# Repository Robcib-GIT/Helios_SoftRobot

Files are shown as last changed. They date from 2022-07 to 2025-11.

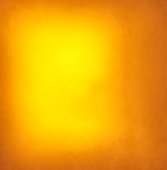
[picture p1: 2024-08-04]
Media/Imágenes/Sensor/WaveGuides/MatlabAnalysis/Core_45.png

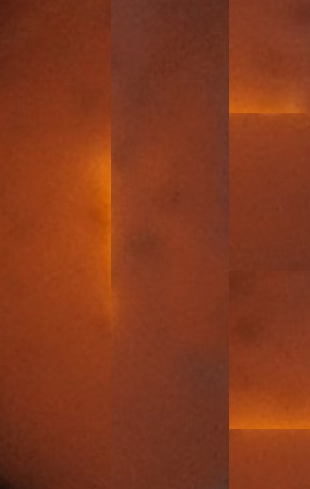
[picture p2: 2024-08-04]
Media/Imágenes/Sensor/WaveGuides/MatlabAnalysis/Cladding_60.png

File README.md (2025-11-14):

**Helios SoftRobot**
=====================================
Demo

**Installation and Configuration**
-------------------------------

### Step 1: Clone the Helios repository

Clone the Helios repository using Git:

```bash
git clone https://github.com/JaimeBravoAlgaba/Helios_SoftRobot.git
```

### Step 2: Create a ROS2 workspace

Create a directory for the ROS2 workspace and make sure it's empty:

```bash
mkdir -p helios_ws/src
```

### Step 3: Install the helios_robot package in the workspace

Copy the helios_robot package to the ROS2 workspace:

```bash
cp -r Helios_SoftRobot/Código/helios_robot helios_ws/src
cd helios_ws/src
```

### Step 4: Install the micro_ros_setup package

Clone the micro_ros_setup repository and make sure it's on the branch corresponding to your ROS2 version:

```bash
git clone https://github.com/micro-ROS/micro_ros_setup.git -b $ROS_DISTRO
cd ..
```

### Step 5: Build the workspace

Update dependencies and build the ROS2 workspace:

```bash
rosdep update && rosdep install --from-paths src --ignore-src -y
colcon build --symlink-install
source install/local_setup.bash
```

### Step 6: Create a MicroROS agent

Create a MicroROS agent and configure the environment:

```bash
ros2 run micro_ros_setup create_agent_ws.sh
ros2 run micro_ros_setup build_agent.sh
source install/local_setup.sh
```

### Step 7: Connect to the ESP32 and run the agent

Change your IP address to 192.168.2.76:



Turn on the robot if you haven't already.

**Terminal Control**
-----------
- You can use the helios_robot.sh file to automatically launch the necessary nodes:
```bash
# Launches the MicroROS agent, kinematics and pose prediction
# In the folder where the file is located, run:
./helios_robot.sh
```
and immediately after, click the RESET button on the ESP32.

- Launch the visualization node:
```bash
ros2 run helios_robot helios_robot_plot
```

- Control the cable lengths, in meters:
```bash
# [L00, L01, L02, L03, L10, L11, ... L22, L23]
ros2 topic pub --once /helios_cables_cmd std_msgs/msg/Float32MultiArray "data: [0,0,0,0,  0,0,0,0,  0,0,0,0]"
```

- Send command in theta and phi coordinates, in radians:
```bash
# [th0, th1, th2, phi0, phi1, phi2]
ros2 topic pub --once /helios_sections_cmd std_msgs/msg/Float32MultiArray "data: [0,0,0,  0,0,0]"
```

- Control the tool (value from 0 to 255):
```bash
ros2 topic pub --once /helios_tool_cmd std_msgs/msg/Int8 "data: 127"
```

### Alternative: Connect to ESP32 via USB

You can use the Helios with a USB cable:
Connect the ESP32 to the USB port and upload the esp32 project after uncommenting the lines that allow serial connection in "main.cpp" and changing board_microros_transport to "serial" in the platformio.ini file

Run the MicroROS agent with:

```bash
ros2 run micro_ros_agent micro_ros_agent serial --dev /dev/ttyUSB0
```

### Common Error Resolution

If an error appears when connecting the ESP32, make sure to grant your user access to the ttyUSB0 USB port:

1. Check the user group that has access to the port:
```bash
stat /dev/ttyUSB0
```

It should show something like: "Gid: (   20/ dialout)"

2. Add your user to the "dialout" group or whichever group appeared:
```bash
sudo usermod -a -G dialout $USER
```
3. Grant read and write permissions to the port:
```bash
sudo chmod a+rw /dev/ttyUSB0
```

After resetting the ESP32, its topics should be visible from another terminal.

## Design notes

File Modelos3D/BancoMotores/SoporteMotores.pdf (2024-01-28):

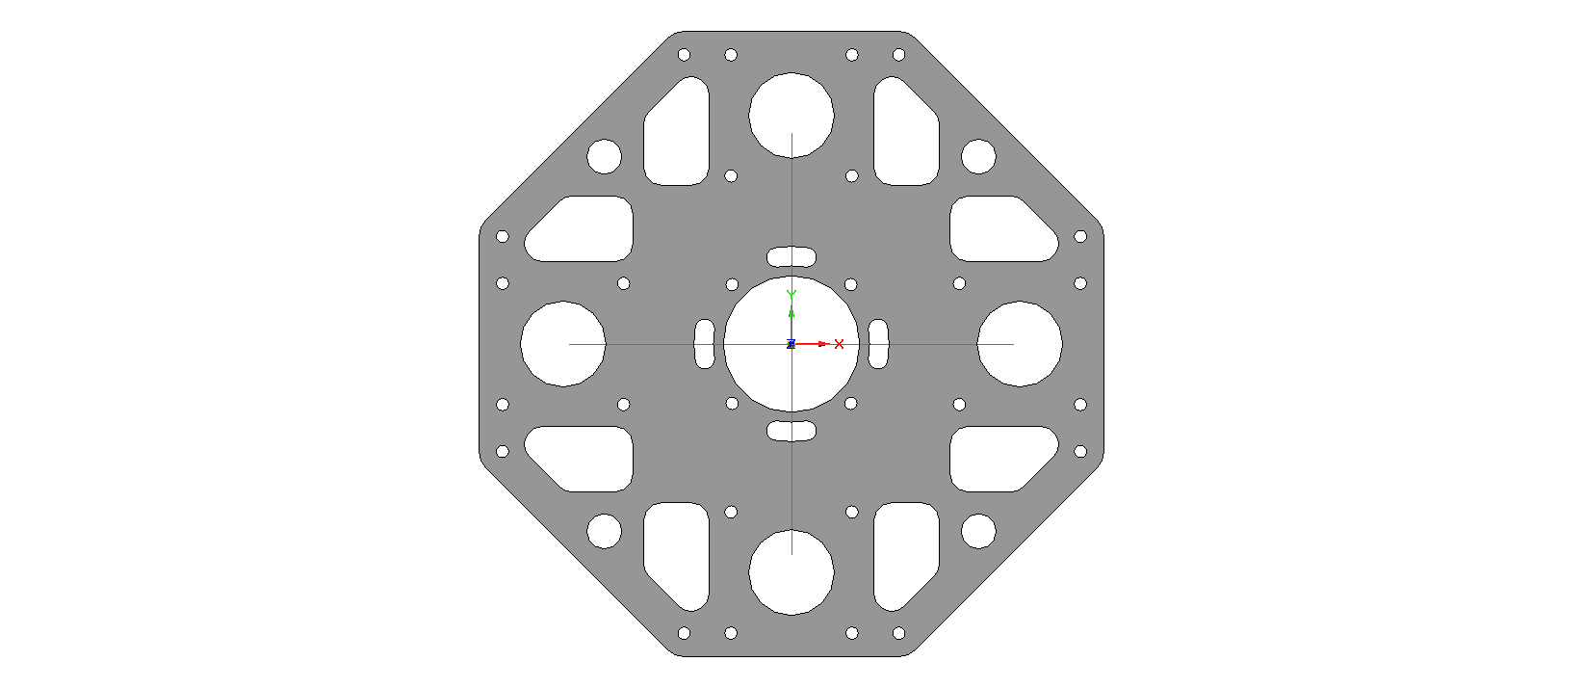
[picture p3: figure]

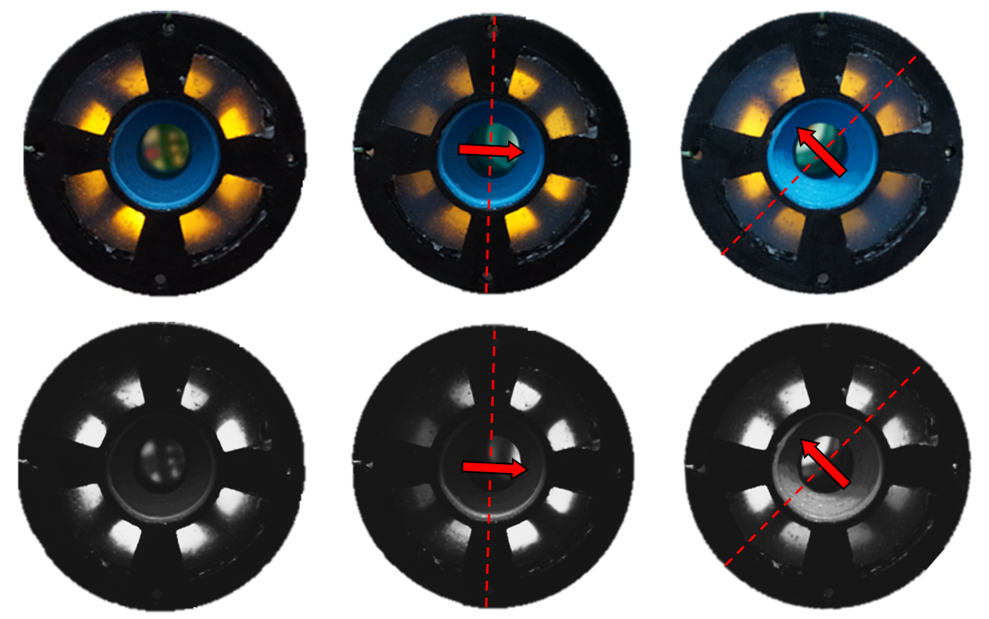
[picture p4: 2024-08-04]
Media/Imágenes/Sensor/HeliosConcept.png

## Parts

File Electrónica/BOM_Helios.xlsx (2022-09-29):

HELIOS MODULE - BOM |  |  |  |  |  |  | EMITTER PCBs |  |  |  | 20
 |  |  |  |  |  |  | RECEIVER PCBs |  |  |  | 20
COMPONENT | PCB | DESCRIPTION | DATASHEET | QTTY. PER CIRCUIT | QTTY. TOTAL | QTTY. PER ORDER | TO ORDER | ORDER PRICE | SHIPPING COSTS | TOTAL PRICE | LINK
OPA2380 | RECEIVER | Transimpedance Amplifier | opa2380 | 2 | 40 | 10 | 4 | 12.77 | 0 | 51.08 | https://es.aliexpress.com/item/1005002651519658.html?curPageLogUid=3uJtDoBWpShc
SFH2704 | RECEIVER | Photodiode | sfh2704 | 4 | 80 | 20 | 4 | 29.12 |  | 116.48 | https://es.rs-online.com/web/p/circuitos-integrados-de-sensores-biometricos/1816802
2M RESISTOR | RECEIVER | Sensing Resistance |  | 4 | 80 |  | 0 | 0 | 0
OA3400 | EMITTER | Logic Level Mosfet | oa3400 | 1 | 20 | 50 | 1 | 0.91 | 1.1 | 2.01 | https://es.aliexpress.com/item/1005004174298809.html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
2K RESISTOR | EMITTER | Pulldown Resistance |  | 1 | 20 |  | 0 | 0 | 0 | 0
241 RESISTOR | EMITTER | Current Limiting Resistance |  | 1 | 20 |  | 0 | 0 | 0 | 0

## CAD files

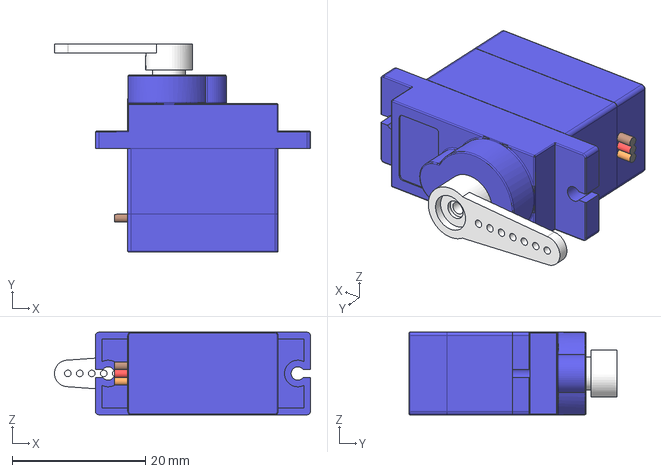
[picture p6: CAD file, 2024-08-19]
Modelos3D/Std_parts/tower-pro-sg90-micro-servo-2.snapshot.8/STEP/microservoAssembly_A3.step
38.4 x 31.3 x 12.4 mm
microservoSG90
microservoArm_A2

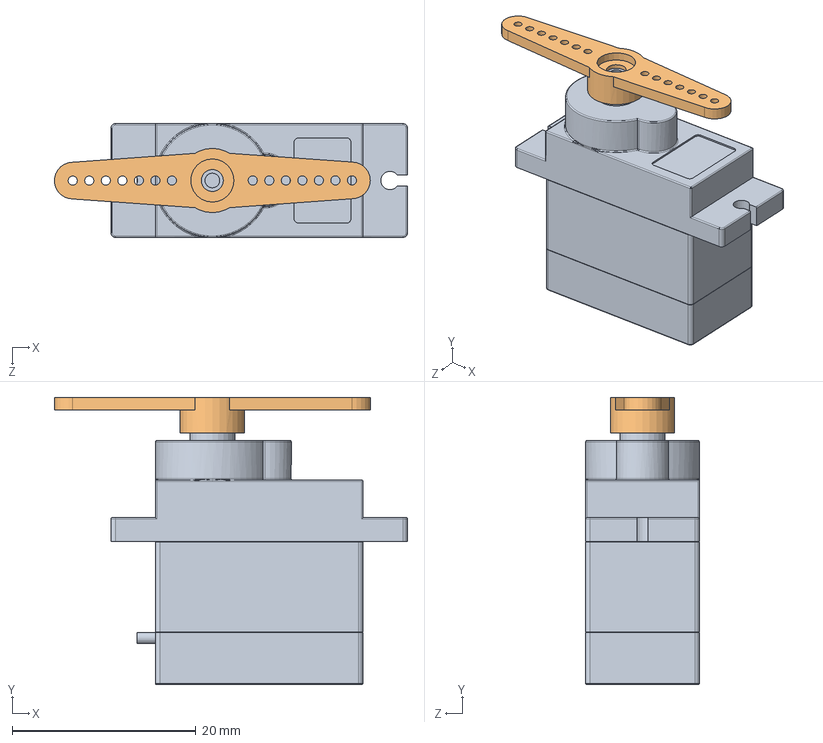
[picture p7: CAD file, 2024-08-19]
Modelos3D/Std_parts/tower-pro-sg90-micro-servo-2.snapshot.8/SLD/microservoAssembly.SLDASM
38.4 x 31.3 x 12.4 mm
microservoSG90
microservoArm

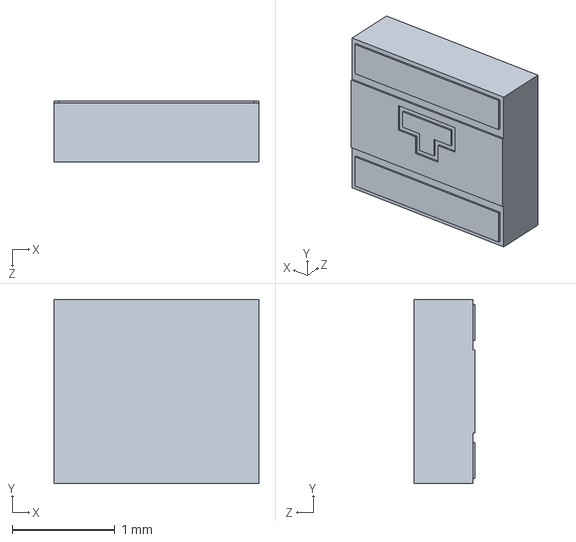
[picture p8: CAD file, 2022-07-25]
Electrónica/KicadLibs/Helios/3dmodels/SFH_2704_20190402_geometry.STEP
2.00 x 1.80 x 0.6 mm

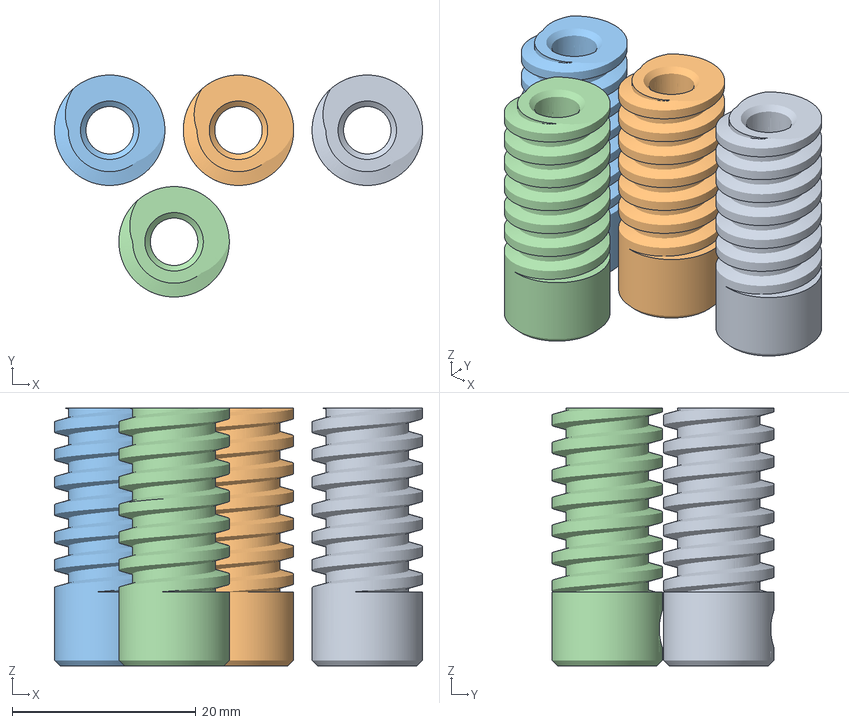
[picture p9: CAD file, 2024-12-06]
Modelos3D/Actuador/STL/CE3PRO_worm_gear.3mf
40.0 x 24.1 x 28.0 mm
worm_gear.stl x 4

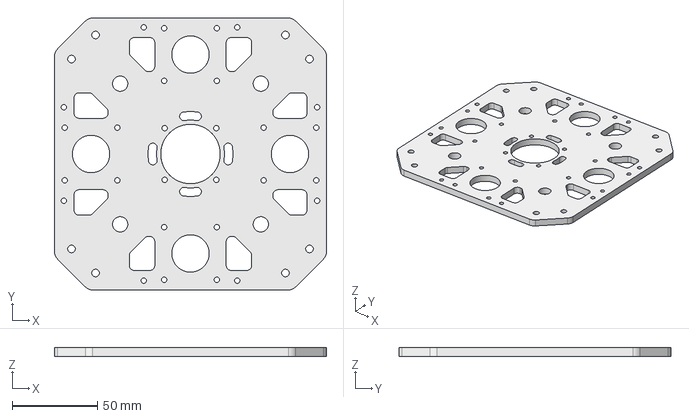
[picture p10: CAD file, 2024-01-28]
Modelos3D/BancoMotores/SoporteMotores.stp
160.0 x 160.0 x 5.00 mm

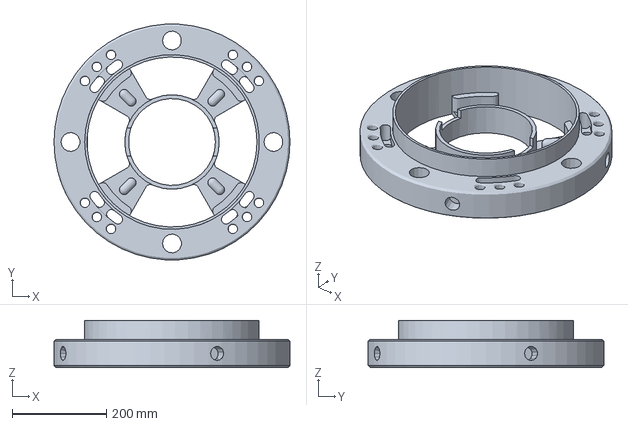
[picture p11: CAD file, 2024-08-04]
Modelos3D/Modulo_Helios/Helios_Disk/STL/MeshBody1.3mf
500.0 x 499.0 x 100.0 mm

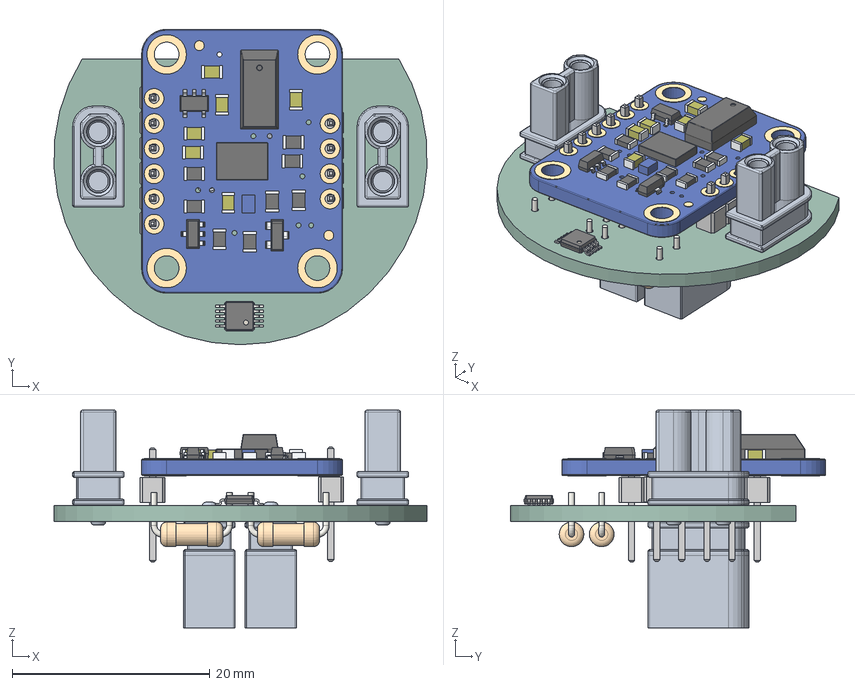
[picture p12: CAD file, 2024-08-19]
Modelos3D/Modulo_IMU/STEP/Helios_IMU_M.step
37.7 x 31.9 x 22.0 mm
ASSEMBLY x 4
(Sin guardar)
MSOP_10_3x3mm_P05mm
R_Axial_DIN0207_L63mm_D25mm_P762mm_Horizontal x 4
Helios_IMU_M_PCB

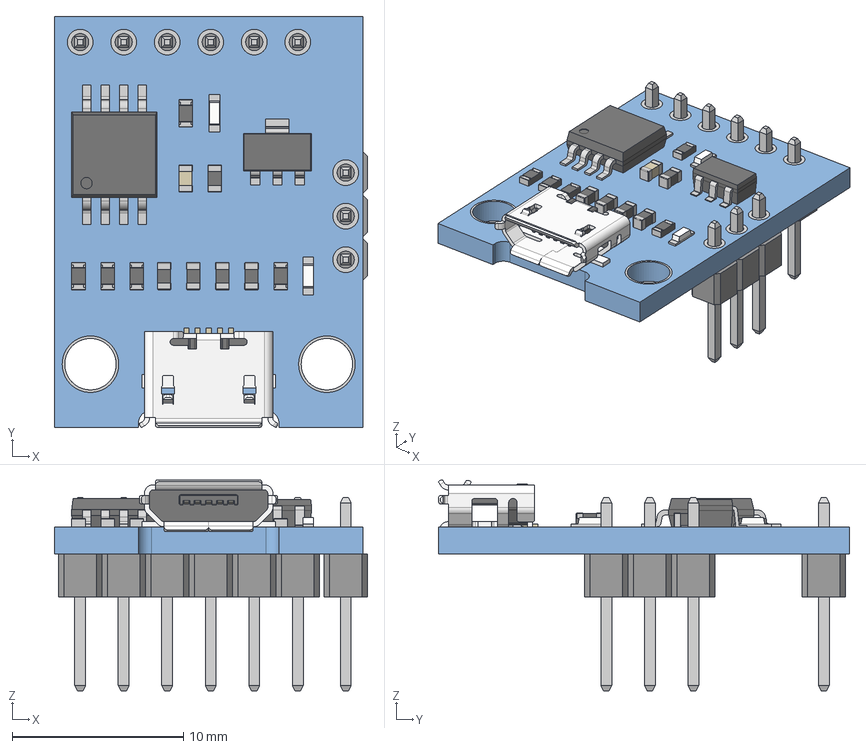
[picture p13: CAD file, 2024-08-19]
Modelos3D/Std_parts/Digispark Attiny85/STEP/Digispark Attiny85 (with pin headers).step
18.3 x 24.0 x 12.3 mm
Pads B
Pads F
Plastic
Pins
Micro USB

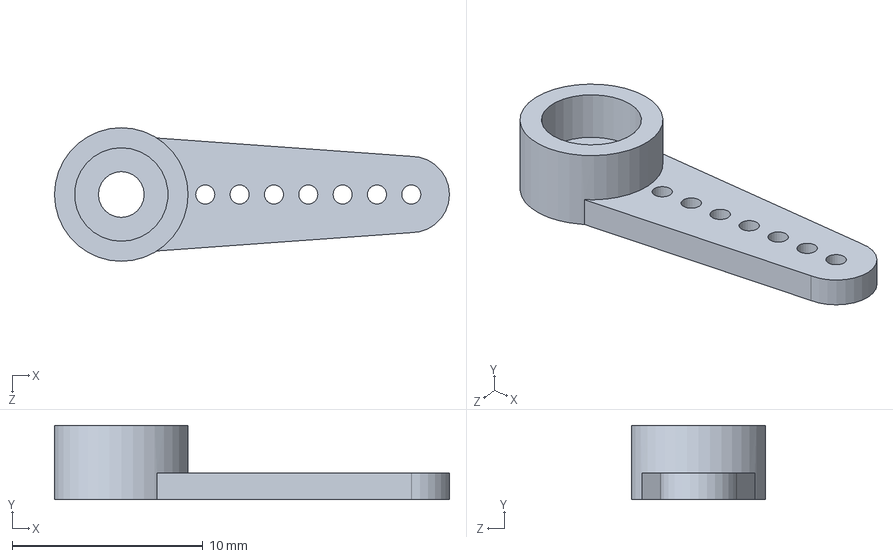
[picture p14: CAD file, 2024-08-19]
Modelos3D/Std_parts/tower-pro-sg90-micro-servo-2.snapshot.8/SLD/microservoArm.SLDPRT
20.7 x 3.90 x 7.00 mm

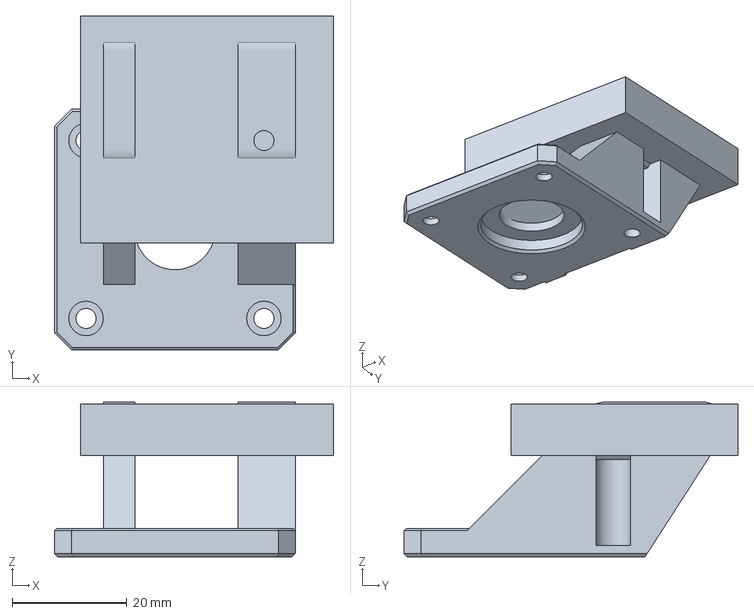
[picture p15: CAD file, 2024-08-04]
Modelos3D/Actuador/STL/CE3PRO_bastidor.3mf
48.6 x 58.2 x 27.0 mm

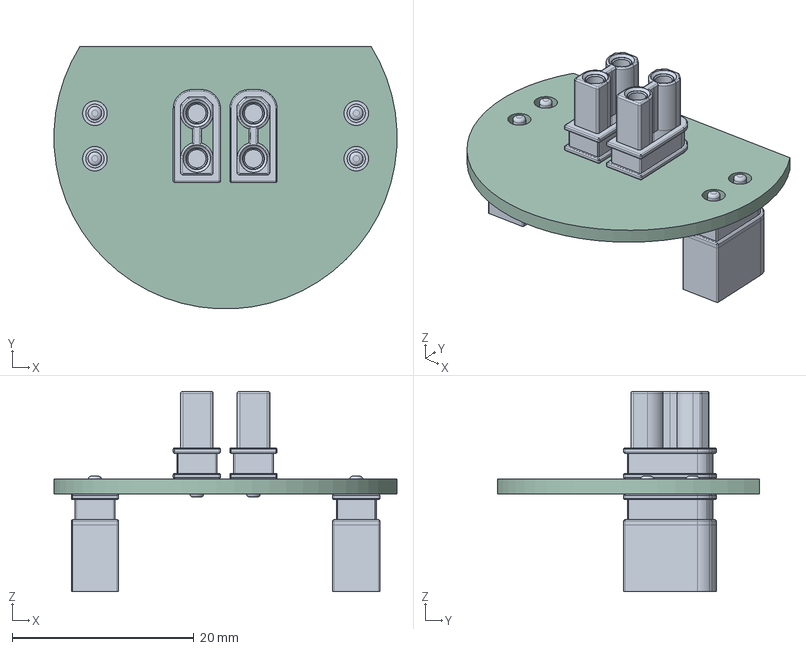
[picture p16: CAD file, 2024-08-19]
Modelos3D/Modulo_IMU/STEP/Helios_IMU_F.step
37.7 x 28.9 x 22.0 mm
ASSEMBLY x 4
Helios_IMU_F_PCB

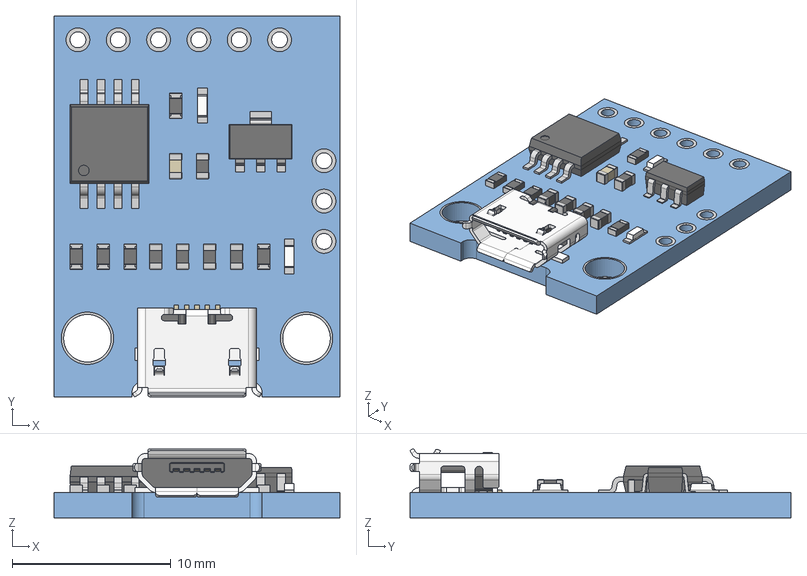
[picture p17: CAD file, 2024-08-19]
Modelos3D/Std_parts/Digispark Attiny85/STEP/Digispark Attiny85.step
18.0 x 24.0 x 4.33 mm
Pads B
Pads F
Micro USB

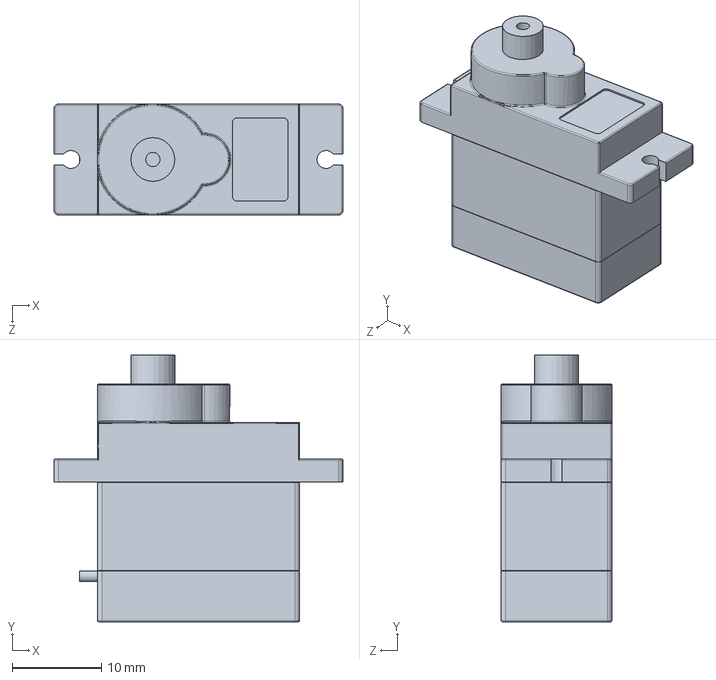
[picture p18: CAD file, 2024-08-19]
Modelos3D/Std_parts/tower-pro-sg90-micro-servo-2.snapshot.8/SLD/microservoSG90.SLDPRT
32.3 x 29.8 x 12.4 mm

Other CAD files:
Modelos3D/Std_parts/tower-pro-sg90-micro-servo-2.snapshot.8/STEP/microservoAssembly.STEP
Modelos3D/BancoMotores/SoporteMotores.dxf

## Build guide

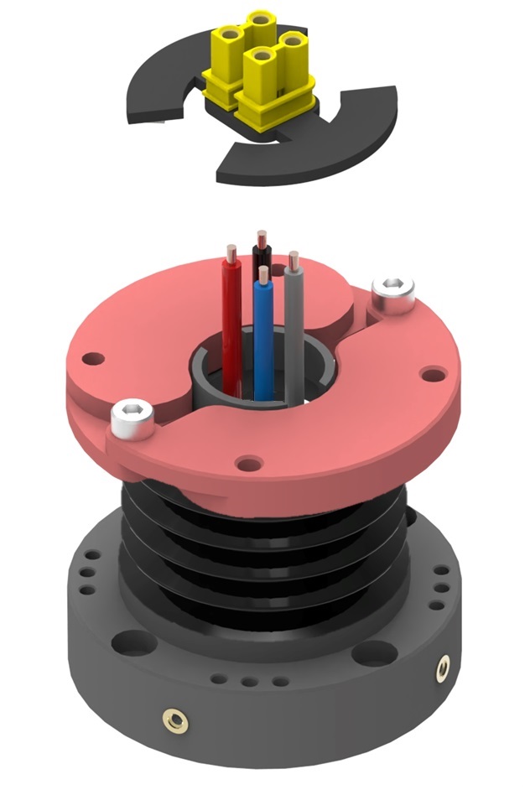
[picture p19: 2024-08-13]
Media/Imágenes/Sensor/Montaje/Paso8_A.jpg

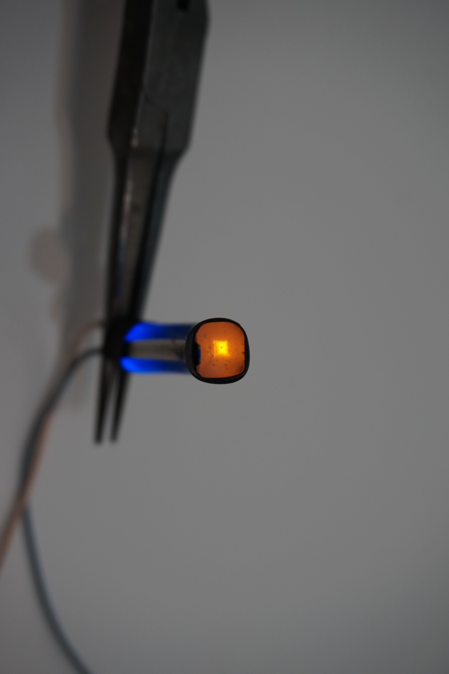
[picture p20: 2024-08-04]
Media/Imágenes/Sensor/WaveGuides/DSC03763.JPG

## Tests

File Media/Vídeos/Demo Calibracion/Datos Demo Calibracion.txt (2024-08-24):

882944,883712,882944,883456,883712,884736,885760,813056,813056,813312,813056,813312,813056,813312,813056,813824,814080,816384,818944,Motor 0 ready!
1333504,1333248,1332992,1333248,1332992,1332992,1333248,1332992,1332992,1333248,1332992,1332736,1333504,1333504,1333504,1333760,1333248,1334528,1333760,1334528,1334016,1334528,1334784,1335808,1337856,1338880,1340928,Motor 1 ready!
884992,884224,885248,884480,884480,884480,885248,885248,886272,886272,887040,887040,888320,889088,891392,Motor 2 ready!
1058304,1057536,1057792,1057536,1057536,1057280,1057792,1057536,1057792,1056768,1056768,1056512,1057792,1057536,1058048,1058048,1059584,1061376,1063168,1064192,Motor 3 ready!

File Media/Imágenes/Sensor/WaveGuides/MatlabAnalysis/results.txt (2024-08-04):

Cladding_0:126.9278
Cladding_30:97.4177
Cladding_45:86.1797
Cladding_60:76.6126
Cladding_90:45.3909
Core_0: 241.5301
Core_30:181.4205
Core_45:170.0201
Core_60:151.1259
Core_90: 94.1238

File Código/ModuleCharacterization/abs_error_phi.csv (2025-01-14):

abs_error_phi
0.26116795148977
0.04501494245398607
0.0574410258210063
0.020018695222546956
0.016932466154500503
0.013030634793675722
0.034537307033584375
0.15690723569580212
0.320014201653114
0.18757705869114538
0.09440884280808515
0.0368035878317714
0.02983785086261359
0.05580359213176056
0.0020724627015749064
0.009271791450760958
0.030697243953760056
0.019202026811451667
0.4846356430390659
0.24310086543101272
0.3646036226921556
0.20089068637257523
0.3063101115709264
0.0775011550070312
0.11384108105206836
0.1928912681536869
0.2883201347980088
0.1947866617707802
0.7724826445851589
0.21229730627382004
0.9380536972626659
0.37003076322835593
0.20886434234514173
0.03226619005276632
0.005806132350358872
0.006876534570471549
0.11219196843804813
0.2676178523780841
0.6903497831046854
0.19649137351556645
0.8923990679322125
1.8585366202787892
0.851094795704527
0.2869960545398129
0.2340101838150428
0.36409824238420363
0.619052754296189
2.541629903082378
1.4491087320107696
0.2106107012452978
0.7238617575863464
0.7805232755565461
0.26711418330450654
0.09001383140166608
0.062076002052634305
0.06536299224974185
0.1192687490245623
0.9140478307294937
0.937242972895965
0.279385629416411
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

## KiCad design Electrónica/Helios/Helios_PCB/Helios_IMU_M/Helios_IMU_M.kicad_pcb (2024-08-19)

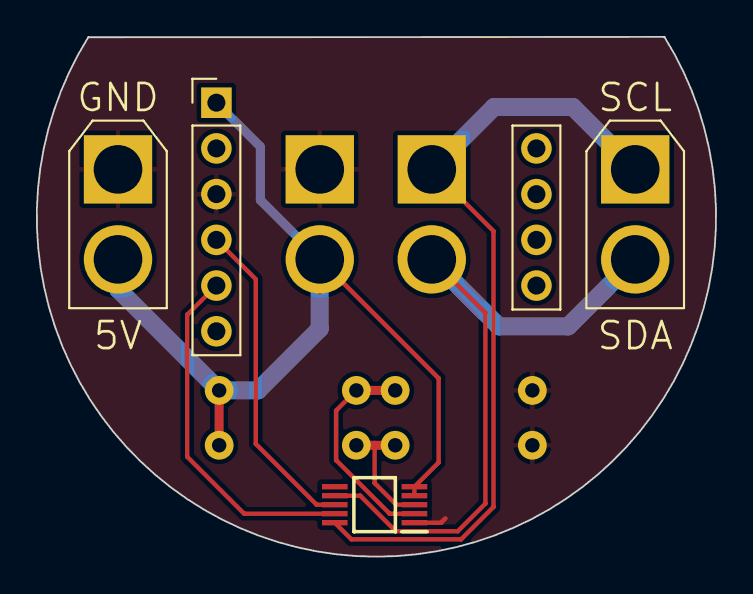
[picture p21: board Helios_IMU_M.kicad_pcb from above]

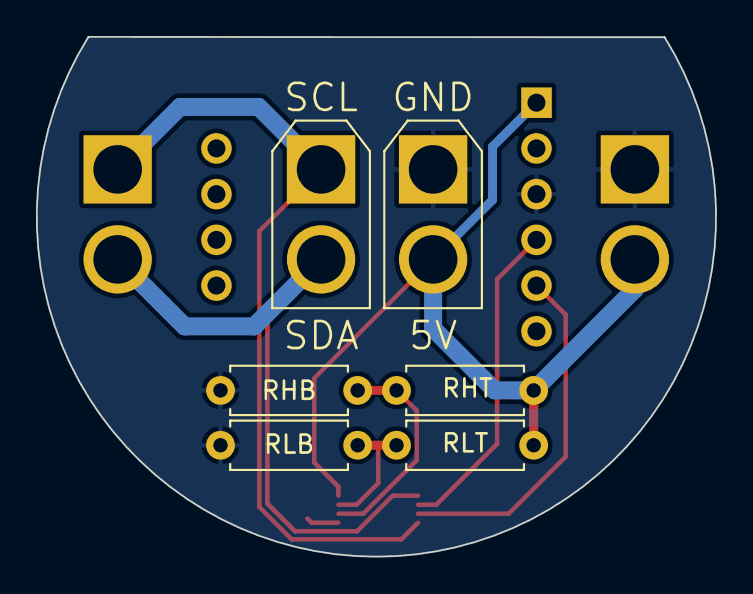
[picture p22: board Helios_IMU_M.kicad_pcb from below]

Board: 2 copper layers, 37.7 x 28.9 mm, 10 parts (6 on the bottom side), 8 nets.

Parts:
IMU1: BNO_055
J1, J2, J3, J4: Conn_01x02_Pin; XT30U-M_1x02_P5.0mm_Vertical
LTC4316: LTC4316CMS#PBF; SOP50P490X110-10N
RHB: R; R_Axial_DIN0207_L6.3mm_D2.5mm_P7.62mm_Horizontal
RHT: R; R_Axial_DIN0207_L6.3mm_D2.5mm_P7.62mm_Horizontal
RLB: R; R_Axial_DIN0207_L6.3mm_D2.5mm_P7.62mm_Horizontal
RLT: R; R_Axial_DIN0207_L6.3mm_D2.5mm_P7.62mm_Horizontal

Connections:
GND: IMU1.3 (GND), J1.1, J3.1, LTC4316.1 (GND), RHB.2, RLB.2
SCL: J2.1, J4.1, LTC4316.10 (SCLIN)
SCL_OUT: IMU1.5 (SCL), LTC4316.9 (SCLOUT)
SDA: J2.2, J4.2, LTC4316.7 (SDAIN)
SDA_OUT: IMU1.4 (SDA), LTC4316.8 (SDAOUT)
VCC: IMU1.1 (Vin), J1.2, J3.2, LTC4316.4 (VCC), LTC4316.5 (ENABLE), RHT.1, RLT.1
XORH: LTC4316.2 (XORH), RHB.1, RHT.2
XORL: LTC4316.3 (XORL), RLB.1, RLT.2

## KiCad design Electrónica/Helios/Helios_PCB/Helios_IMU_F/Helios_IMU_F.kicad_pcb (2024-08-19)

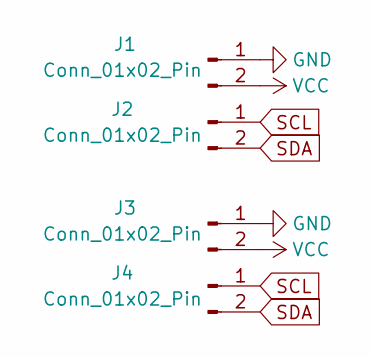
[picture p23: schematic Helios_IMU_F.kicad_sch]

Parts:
J1, J2, J3, J4: Conn_01x02_Pin; XT30U-M_1x02_P5.0mm_Vertical

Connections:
GND: J1.1, J3.1
SCL: J2.1, J4.1
SDA: J2.2, J4.2
VCC: J1.2, J3.2

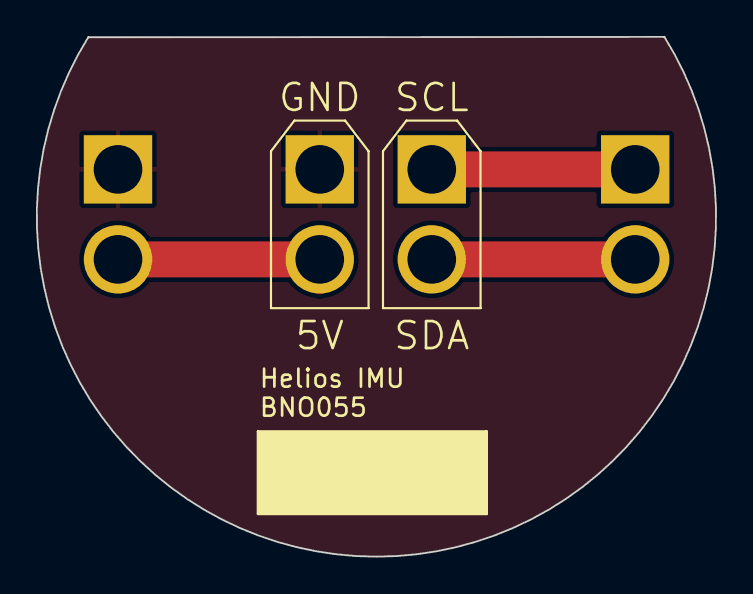
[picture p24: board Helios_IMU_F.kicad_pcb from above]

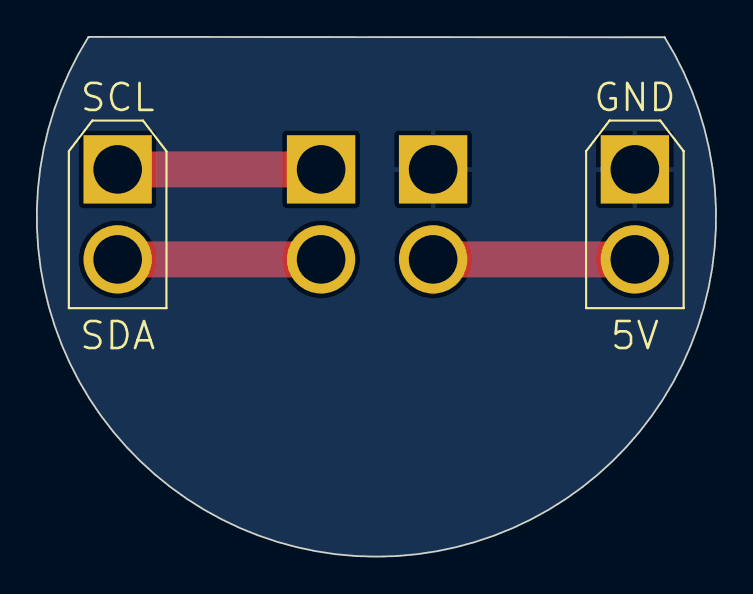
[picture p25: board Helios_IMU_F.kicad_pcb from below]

Board: 2 copper layers, 37.7 x 28.9 mm, 4 parts (2 on the bottom side), 4 nets.

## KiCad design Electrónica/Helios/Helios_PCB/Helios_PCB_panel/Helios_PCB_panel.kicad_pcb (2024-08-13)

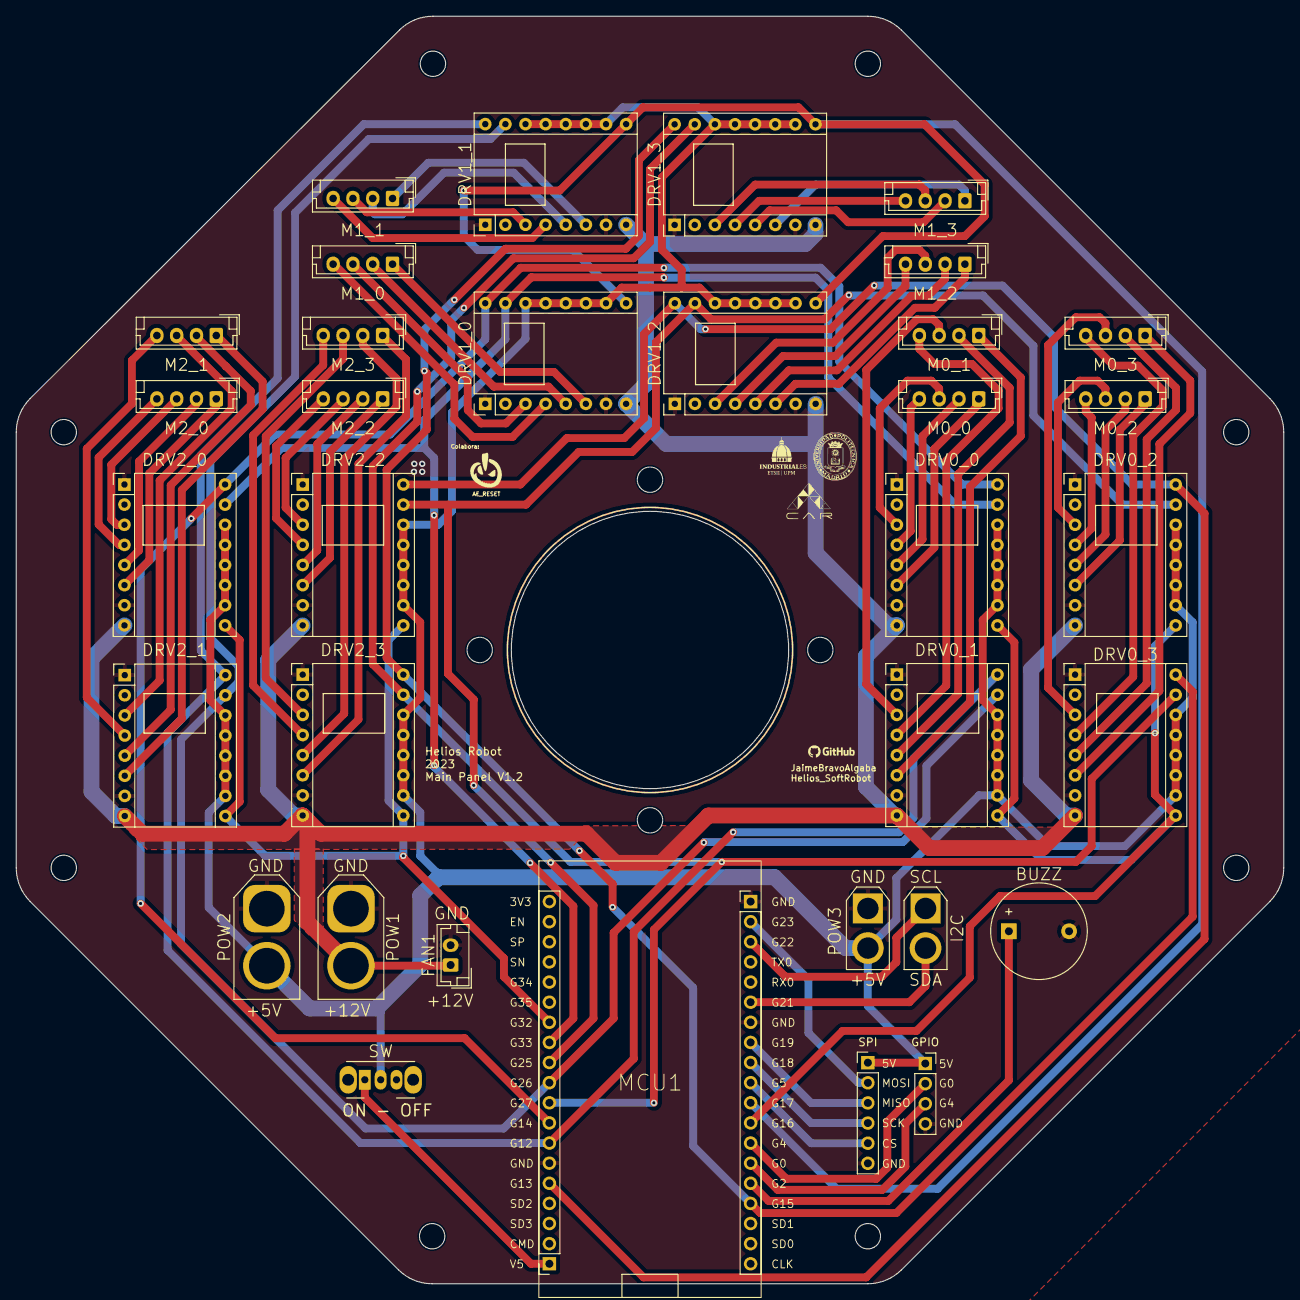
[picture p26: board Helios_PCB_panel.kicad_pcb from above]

Board: 2 copper layers, 160.0 x 160.0 mm, 46 parts (0 on the bottom side), 72 nets.

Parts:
BUZZ: Buzzer; Buzzer_12x9.5RM7.6
DRV0_0, DRV0_1, DRV0_2, DRV0_3, DRV1_0, DRV1_1, DRV1_2, DRV1_3, DRV2_0, DRV2_1, DRV2_2, DRV2_3: Pololu_Breakout_DRV8825; Pololu_Breakout-16_15.2x20.3mm
FAN1: 12VDC; JST_EH_B2B-EH-A_1x02_P2.50mm_Vertical
GPIO: Conn_01x04_Pin; PinSocket_1x04_P2.54mm_Vertical
H1, H2, H3, H4, H5, H6, H7, H8, H9, H10, H11, H12: MountingHole; MountingHole_3.2mm_M3
I2C: I2C1; XT30U-F_1x02_P5.0mm_Vertical
M0_0, M0_1, M0_2, M0_3, M1_0, M1_1, M1_2, M1_3, M2_0, M2_1, M2_2, M2_3: Conn_01x04_Pin; JST_EH_B4B-EH-A_1x04_P2.50mm_Vertical
MCU1: NodeMCU
POW1: 12VDC; XT60-M_1x02_P7.20mm_Vertical
POW2: 5VDC; XT60-M_1x02_P7.20mm_Vertical
POW3: 5VDC; XT30U-F_1x02_P5.0mm_Vertical
SPI: Conn_01x06_Pin; PinHeader_1x06_P2.54mm_Vertical
SW: SW_SPDT; SW_CuK_OS102011MA1QN1_SPDT_Angled

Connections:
+5V: DRV0_0.10 (M0), DRV0_0.11 (M1), DRV0_0.12 (M2), DRV0_0.13 (~RST), DRV0_0.14 (~SLP), DRV0_1.10 (M0), DRV0_1.11 (M1), DRV0_1.12 (M2), DRV0_1.13 (~RST), DRV0_1.14 (~SLP), DRV0_2.10 (M0), DRV0_2.11 (M1), DRV0_2.12 (M2), DRV0_2.13 (~RST), DRV0_2.14 (~SLP), DRV0_3.10 (M0), DRV0_3.11 (M1), DRV0_3.12 (M2), DRV0_3.13 (~RST), DRV0_3.14 (~SLP), DRV1_0.10 (M0), DRV1_0.11 (M1), DRV1_0.12 (M2), DRV1_0.13 (~RST), DRV1_0.14 (~SLP), DRV1_1.10 (M0), DRV1_1.11 (M1), DRV1_1.12 (M2), DRV1_1.13 (~RST), DRV1_1.14 (~SLP), DRV1_2.10 (M0), DRV1_2.11 (M1), DRV1_2.12 (M2), DRV1_2.13 (~RST), DRV1_2.14 (~SLP), DRV1_3.10 (M0), DRV1_3.11 (M1), DRV1_3.12 (M2), DRV1_3.13 (~RST), DRV1_3.14 (~SLP), DRV2_0.10 (M0), DRV2_0.11 (M1), DRV2_0.12 (M2), DRV2_0.13 (~RST), DRV2_0.14 (~SLP), DRV2_1.10 (M0), DRV2_1.11 (M1), DRV2_1.12 (M2), DRV2_1.13 (~RST), DRV2_1.14 (~SLP), DRV2_2.10 (M0), DRV2_2.11 (M1), DRV2_2.12 (M2), DRV2_2.13 (~RST), DRV2_2.14 (~SLP), DRV2_3.10 (M0), DRV2_3.11 (M1), DRV2_3.12 (M2), DRV2_3.13 (~RST), DRV2_3.14 (~SLP), GPIO.1, POW2.2, POW3.2, SPI.1, SW.2 (B)
+12V: DRV0_0.8 (VMOT), DRV0_1.8 (VMOT), DRV0_2.8 (VMOT), DRV0_3.8 (VMOT), DRV1_0.8 (VMOT), DRV1_1.8 (VMOT), DRV1_2.8 (VMOT), DRV1_3.8 (VMOT), DRV2_0.8 (VMOT), DRV2_1.8 (VMOT), DRV2_2.8 (VMOT), DRV2_3.8 (VMOT), FAN1.1, POW1.2
BUZZ: BUZZ.1 (-), MCU1.24 (G2)
CS: MCU1.29 (G5), SPI.5
D0: DRV0_0.16 (DIR), DRV1_0.16 (DIR), DRV2_0.16 (DIR), MCU1.12 (G14)
D1: DRV0_1.16 (DIR), DRV1_1.16 (DIR), DRV2_1.16 (DIR), MCU1.13 (G12)
D2: DRV0_2.16 (DIR), DRV1_2.16 (DIR), DRV2_2.16 (DIR), MCU1.15 (G13)
D3: DRV0_3.16 (DIR), DRV1_3.16 (DIR), DRV2_3.16 (DIR), MCU1.23 (G15)
EN0: DRV0_0.9 (~EN), DRV0_1.9 (~EN), DRV0_2.9 (~EN), DRV0_3.9 (~EN), MCU1.27 (G16)
EN1: DRV1_0.9 (~EN), DRV1_1.9 (~EN), DRV1_2.9 (~EN), DRV1_3.9 (~EN), MCU1.28 (G17)
EN2: DRV2_0.9 (~EN), DRV2_1.9 (~EN), DRV2_2.9 (~EN), DRV2_3.9 (~EN), MCU1.7 (G32)
GND: BUZZ.2 (+), DRV0_0.1 (GND), DRV0_0.7 (GND), DRV0_1.1 (GND), DRV0_1.7 (GND), DRV0_2.1 (GND), DRV0_2.7 (GND), DRV0_3.1 (GND), DRV0_3.7 (GND), DRV1_0.1 (GND), DRV1_0.7 (GND), DRV1_1.1 (GND), DRV1_1.7 (GND), DRV1_2.1 (GND), DRV1_2.7 (GND), DRV1_3.1 (GND), DRV1_3.7 (GND), DRV2_0.1 (GND), DRV2_0.7 (GND), DRV2_1.1 (GND), DRV2_1.7 (GND), DRV2_2.1 (GND), DRV2_2.7 (GND), DRV2_3.1 (GND), DRV2_3.7 (GND), FAN1.2, GPIO.4, MCU1.14 (GND), MCU1.32 (GND), MCU1.38 (GND), POW1.1, POW2.1, POW3.1, SPI.6
MISO: MCU1.31 (G19), SPI.3
MOSI: MCU1.37 (G23), SPI.2
unnamed: DRV0_0.4 (A1), M0_0.4
unnamed: DRV0_0.3 (A2), M0_0.3
unnamed: DRV0_0.5 (B1), M0_0.2
unnamed: DRV0_0.6 (B2), M0_0.1
unnamed: DRV0_1.4 (A1), M0_1.4
unnamed: DRV0_1.3 (A2), M0_1.3
unnamed: DRV0_1.5 (B1), M0_1.2
unnamed: DRV0_1.6 (B2), M0_1.1
unnamed: DRV0_2.4 (A1), M0_2.4
unnamed: DRV0_2.3 (A2), M0_2.3
unnamed: DRV0_2.5 (B1), M0_2.2
unnamed: DRV0_2.6 (B2), M0_2.1
unnamed: DRV0_3.4 (A1), M0_3.4
unnamed: DRV0_3.3 (A2), M0_3.3
unnamed: DRV0_3.5 (B1), M0_3.2
unnamed: DRV0_3.6 (B2), M0_3.1
unnamed: DRV1_0.4 (A1), M1_0.4
unnamed: DRV1_0.3 (A2), M1_0.3
unnamed: DRV1_0.5 (B1), M1_0.2
unnamed: DRV1_0.6 (B2), M1_0.1
unnamed: DRV1_1.4 (A1), M1_1.4
unnamed: DRV1_1.3 (A2), M1_1.3
unnamed: DRV1_1.5 (B1), M1_1.2
unnamed: DRV1_1.6 (B2), M1_1.1
unnamed: DRV1_2.4 (A1), M1_2.4
unnamed: DRV1_2.3 (A2), M1_2.3
unnamed: DRV1_2.5 (B1), M1_2.2
unnamed: DRV1_2.6 (B2), M1_2.1
unnamed: DRV1_3.4 (A1), M1_3.4
unnamed: DRV1_3.3 (A2), M1_3.3
unnamed: DRV1_3.5 (B1), M1_3.2
unnamed: DRV1_3.6 (B2), M1_3.1
unnamed: DRV2_0.4 (A1), M2_0.4
unnamed: DRV2_0.3 (A2), M2_0.3
unnamed: DRV2_0.5 (B1), M2_0.2
unnamed: DRV2_0.6 (B2), M2_0.1
unnamed: DRV2_1.4 (A1), M2_1.4
unnamed: DRV2_1.3 (A2), M2_1.3
unnamed: DRV2_1.5 (B1), M2_1.2
unnamed: DRV2_1.6 (B2), M2_1.1
unnamed: DRV2_2.4 (A1), M2_2.4
unnamed: DRV2_2.3 (A2), M2_2.3
unnamed: DRV2_2.5 (B1), M2_2.2
unnamed: DRV2_2.6 (B2), M2_2.1
unnamed: DRV2_3.4 (A1), M2_3.4
unnamed: DRV2_3.3 (A2), M2_3.3
unnamed: DRV2_3.5 (B1), M2_3.2
unnamed: DRV2_3.6 (B2), M2_3.1
unnamed: GPIO.2, MCU1.26 (G4)
unnamed: GPIO.3, MCU1.25 (G0)
unnamed: MCU1.19 (V5), SW.1 (A)
S0: DRV0_0.15 (STEP), DRV1_0.15 (STEP), DRV2_0.15 (STEP), MCU1.8 (G33)
S1: DRV0_1.15 (STEP), DRV1_1.15 (STEP), DRV2_1.15 (STEP), MCU1.10 (G26)
S2: DRV0_2.15 (STEP), DRV1_2.15 (STEP), DRV2_2.15 (STEP), MCU1.9 (G25)
S3: DRV0_3.15 (STEP), DRV1_3.15 (STEP), DRV2_3.15 (STEP), MCU1.11 (G27)
SCK: MCU1.30 (G18), SPI.4
SCL: I2C.1, MCU1.36 (G22)
SDA: I2C.2, MCU1.33 (G21)

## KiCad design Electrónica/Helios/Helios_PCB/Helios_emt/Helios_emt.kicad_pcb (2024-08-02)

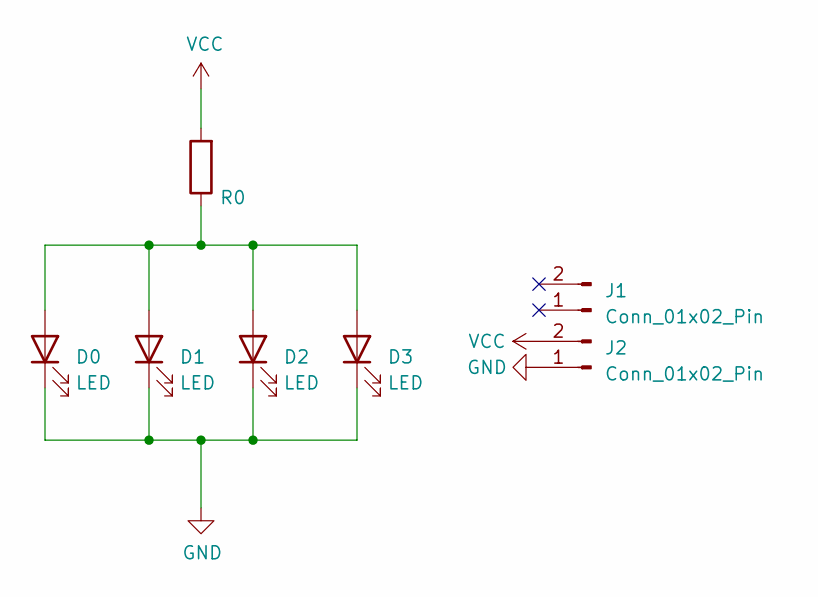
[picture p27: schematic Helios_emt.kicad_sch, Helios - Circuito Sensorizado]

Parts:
D0, D1, D2, D3: LED; LED_PLCC-2
J1, J2: Conn_01x02_Pin; AMASS_XT30U-F_1x02_P5.0mm_Vertical
R0: RL; R_0805_2012Metric

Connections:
GND: D0.1 (K), D1.1 (K), D2.1 (K), D3.1 (K), J2.1
unnamed: D0.2 (A), D1.2 (A), D2.2 (A), D3.2 (A), R0.1
VCC: J2.2, R0.2

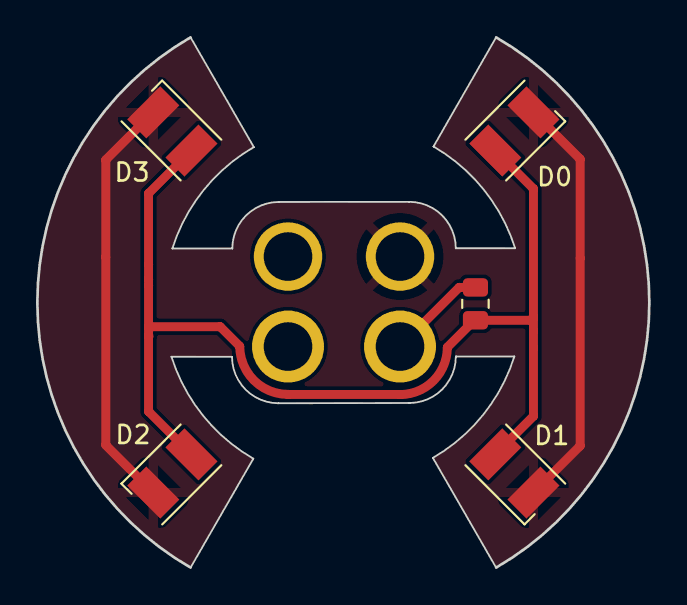
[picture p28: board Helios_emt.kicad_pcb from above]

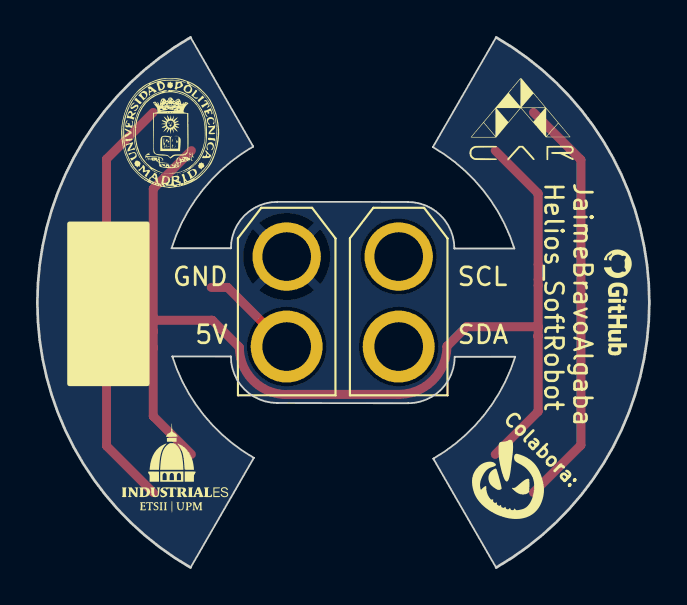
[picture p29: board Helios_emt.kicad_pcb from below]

Board: 2 copper layers, 34.0 x 29.5 mm, 7 parts (2 on the bottom side), 3 nets.

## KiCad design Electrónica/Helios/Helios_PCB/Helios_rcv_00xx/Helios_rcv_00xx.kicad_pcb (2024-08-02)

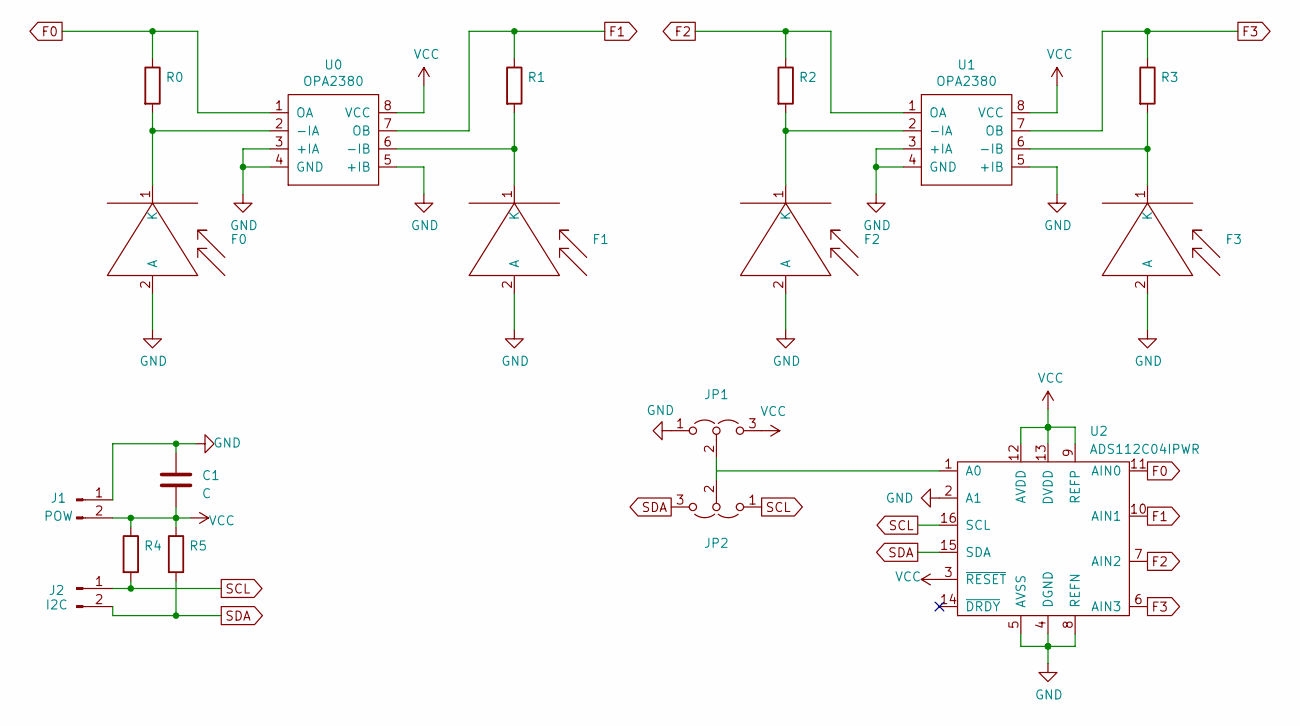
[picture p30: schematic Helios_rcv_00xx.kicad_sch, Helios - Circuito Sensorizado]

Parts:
C1: C; C_0805_2012Metric
F0, F1, F2, F3: SFH2704; SFH2704_Photodiode
J1: POW; XT30U-M_1x02_P5.0mm_Vertical
J2: I2C; XT30U-M_1x02_P5.0mm_Vertical
JP1, JP2: Jumper_3_Open; SolderJumper-3_P1.3mm_Open_Pad1.0x1.5mm
R0, R1, R2, R3, R4, R5: Rf; R_0805_2012Metric
U0, U1: OPA2380
U2: ADS112C04IPWR; TSSOP-16_4.4x5mm_P0.65mm

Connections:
F0: R0.1, U0.1 (OA), U2.11 (AIN0)
F1: R1.1, U0.7 (OB), U2.10 (AIN1)
F2: R2.1, U1.1 (OA), U2.7 (AIN2)
F3: R3.1, U1.7 (OB), U2.6 (AIN3)
GND: C1.1, F0.2 (A), F1.2 (A), F2.2 (A), F3.2 (A), J1.1, JP1.1 (A), U0.3 (+IA), U0.4 (GND), U0.5 (+IB), U1.3 (+IA), U1.4 (GND), U1.5 (+IB), U2.2 (A1), U2.4 (DGND), U2.5 (AVSS), U2.8 (REFN)
unnamed: F0.1 (K), R0.2, U0.2 (-IA)
unnamed: F1.1 (K), R1.2, U0.6 (-IB)
unnamed: F2.1 (K), R2.2, U1.2 (-IA)
unnamed: F3.1 (K), R3.2, U1.6 (-IB)
unnamed: JP1.2 (C), JP2.2 (C)
SCL: J2.1, JP2.1 (A), R4.2, U2.16 (SCL)
SDA: J2.2, JP2.3 (B), R5.2, U2.15 (SDA)
VCC: C1.2, J1.2, JP1.3 (B), R4.1, R5.1, U0.8 (VCC), U1.8 (VCC), U2.3 (~RESET), U2.9 (REFP), U2.12 (AVDD), U2.13 (DVDD)

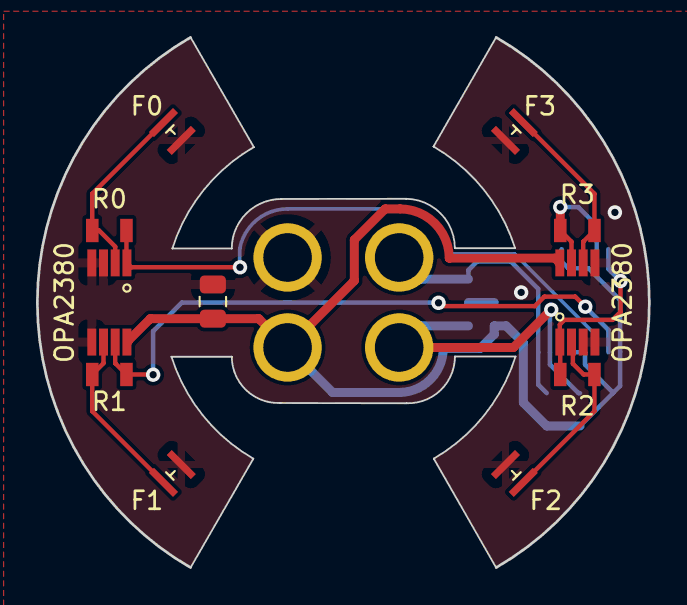
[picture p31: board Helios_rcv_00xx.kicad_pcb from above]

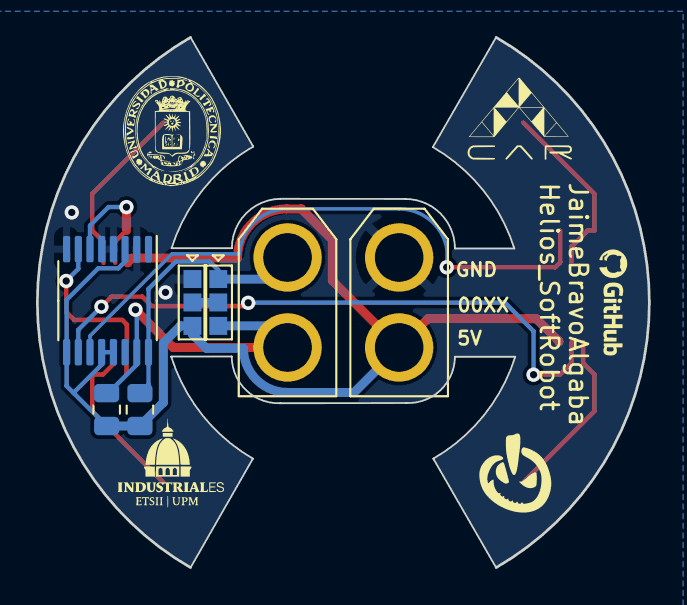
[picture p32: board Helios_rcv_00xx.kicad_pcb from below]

Board: 2 copper layers, 34.0 x 29.5 mm, 18 parts (7 on the bottom side), 13 nets.

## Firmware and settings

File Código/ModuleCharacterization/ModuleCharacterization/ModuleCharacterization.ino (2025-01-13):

#include <Wire.h>
#include "CNC_Shield_UNO.h"
#include "Helios.h"

#define HELIOS_ADDR 0x4A
#define IMU_0_ADDR 0x08
#define TCA_ADDR 0x70

HeliosSensor helios;
Adafruit_VL6180X tof = Adafruit_VL6180X();

uint32_t h[4] = {0, 0, 0, 0}; // Helios module measurement
uint8_t l_tofs[4]; // TOF modules measurement

float cableLengths[4] = {SEGMENTS_LEN, SEGMENTS_LEN, SEGMENTS_LEN, SEGMENTS_LEN};
sensors_event_t orientationData;

CoordsPCC coords_ref;
CoordsPCC coords_meas;

bool succ_init = true;

void move(CoordsPCC c) {
  float l_ref[4] = {0, 0, 0, 0};
  long dn[4] = {0, 0, 0, 0};
  
  for (uint8_t i = 0; i < 4; ++i) {
    l_ref[i] = cableIKine(c, i);
    dn[i] = length2steps(l_ref[i] - cableLengths[i]);
    cableLengths[i] = l_ref[i];
  }
  stepParallel(dn);
}

void calibrateCables() {
  print_info("Starting calibration... ");
  
  // De-tension the cables lengthening them
  long dn[4] = {length2steps(0.005), length2steps(0.005), length2steps(0.005), length2steps(0.005)};
  stepParallel(dn);
  
  memmove(l_tofs, readTOFs(), sizeof(l_tofs) * sizeof(uint8_t));
  long l_tofs_init[4];
  for (uint8_t i = 0; i < 4; ++i) {
    dn[i] = 0;
  }
  
  for(uint8_t i = 0; i < 4; ++i) {
    dn[i] = length2steps(-0.001);
    l_tofs_init[i] = l_tofs[i];

    while (abs(l_tofs[i] - l_tofs_init[i]) < 3) {
      stepParallel(dn);
      memmove(l_tofs, readTOFs(), sizeof(l_tofs) * sizeof(uint8_t));
    }
    dn[i] = 0;
  }

  coords_meas = tofs2pcc(l_tofs[0], l_tofs[1], l_tofs[2], l_tofs[3]);
}

void printData() {
  // Print TOF data
  Serial.print("{\"TOFS\":[");
  for (uint8_t i = 0; i < 3; ++i) {
    Serial.print(l_tofs[i]);
    Serial.print(",");
  }
  Serial.print(l_tofs[3]);

  // Print Helios data
  Serial.print("], \"HELIOS\":[");
  for (uint8_t i = 0; i < 4; ++i) {
    Serial.print(h[i]);
    if (i < 3) {
      Serial.print(",");
    } else {
      Serial.print("]}\n");
    }
  }
}

void setup() {
  setupCNC();

  Serial.begin(115200);
  while (!Serial) delay(10);  // Wait for serial port to open
  Wire.begin();

  // HELIOS INIT
  print_info("Initializing Helios module on address ");
  print_info(String(HELIOS_ADDR));
  print_info("\n");
  while (!helios.begin(HELIOS_ADDR)) {
    print_info(F("Helios Module not detected. Retrying...\n"));
    delay(500);
  }

  helios.configureADCmode(ADS122C04_RAW_MODE);
  helios.setGain(ADS122C04_GAIN_128);
  helios.setConversionMode(ADS122C04_CONVERSION_MODE_CONTINUOUS);
  helios.start();

  print_info("OK\n");

  // TCA9548A Initialization
  print_info("Initializing TCA9548A with address ");
  print_info(String(TCA_ADDR));
  print_info("\n");
  
  for (uint8_t i = 0; i < 4; ++i) {
    tcaSelect(i);
    if (!tof.begin()) {
      print_info(F("\tFailed to boot TOF on channel "));
      print_info(String(i));
      print_info("\n");
      succ_init = false;
    } else {
      print_info(F("\tSuccess booting TOF on channel "));
      print_info(String(i));
      print_info("\n");
    }
  }
  print_info("OK\n");

  if (succ_init) {  
    print_info("\nInitialization successful!\n");
  } else {
    print_info("\nInitialization failed!\n");
    while (1);
  }

  Serial.println("START");
}

void loop() {  
  if (Serial.available() > 0) {
    String cmd = Serial.readStringUntil('\n');

    if (cmd == "HELLO") {
      Serial.println("OK");
      return;
    }
    
    else if (cmd == "CALIBRATE") {
      calibrateCables();
      Serial.println("OK");
    }
    
    else {
      float dl[4];
      long dn[4];

      if (cmd.startsWith("DELTA_LEN:")) {
        cmd.remove(0, String("DELTA_LEN:").length());

        int firstComma  = cmd.indexOf(',');
        int secondComma = cmd.indexOf(',', firstComma + 1);
        int thirdComma  = cmd.indexOf(',', secondComma + 1);

        int commas[3];
        commas[0] = cmd.indexOf(',');        
        commas[1] = cmd.indexOf(',', commas[0] + 1);
        commas[2] = cmd.indexOf(',', commas[1] + 1);

        dl[0] = cmd.substring(0, commas[0]).toFloat();
        dn[0] = length2steps(dl[0]);
        for (int i = 1; i < 4; ++i) {
          dl[i] = cmd.substring(commas[i - 1] + 1, (i < 3) ? commas[i] : cmd.length()).toFloat();
          dn[i] = length2steps(dl[i]);
          cableLengths[i] = dl[i] + cableLengths[i];
        }
      }

      else if (cmd.startsWith("DELTA_STEPS:")) {
        cmd.remove(0, String("DELTA_STEPS:").length());

        int firstComma  = cmd.indexOf(',');
        int secondComma = cmd.indexOf(',', firstComma + 1);
        int thirdComma  = cmd.indexOf(',', secondComma + 1);
        
        int commas[3];
        commas[0] = cmd.indexOf(',');
        commas[1] = cmd.indexOf(',', commas[0] + 1);
        commas[2] = cmd.indexOf(',', commas[1] + 1);

        dn[0] = cmd.substring(0, commas[0]).toInt();
        for (int i = 1; i < 4; ++i) {
          dn[i] = cmd.substring(commas[i - 1] + 1, (i < 3) ? commas[i] : cmd.length()).toInt();
          dl[i] = steps2length(dn[i]);
          cableLengths[i] = dl[i] + cableLengths[i];
        }   
      }

      else if (cmd.startsWith("DELTA_PCC:")) {
        cmd.remove(0, String("DELTA_PCC:").length());

        int firstComma  = cmd.indexOf(',');
        int secondComma = cmd.indexOf(',', firstComma + 1);
        int thirdComma  = cmd.indexOf(',', secondComma + 1);

        coords_ref.theta = cmd.substring(0, firstComma).toFloat() + coords_meas.theta;
        coords_ref.phi = cmd.substring(firstComma + 1, secondComma).toFloat() + coords_meas.phi;
        coords_ref.length = cmd.substring(secondComma + 1, thirdComma).toFloat() + coords_meas.length;
        
        for (uint8_t i = 0; i < 4; ++i) {
          dl[i] = cableIKine(coords_ref, i) - cableLengths[i];
          dn[i] = length2steps(dl[i]);
          cableLengths[i] = dl[i] + cableLengths[i];
        }
      }

      else if (cmd.startsWith("REF_PCC:")) {
        cmd.remove(0, String("REF_PCC:").length());

        int firstComma  = cmd.indexOf(',');
        int secondComma = cmd.indexOf(',', firstComma + 1);
        int thirdComma  = cmd.indexOf(',', secondComma + 1);

        coords_ref.theta = cmd.substring(0, firstComma).toFloat();
        coords_ref.phi = cmd.substring(firstComma + 1, secondComma).toFloat();
        coords_ref.length = cmd.substring(secondComma + 1, thirdComma).toFloat();
        
        for (uint8_t i = 0; i < 4; ++i) {
          dl[i] = cableIKine(coords_ref, i) - cableLengths[i];
          dn[i] = length2steps(dl[i]);
          cableLengths[i] = dl[i] + cableLengths[i];
        }
      }

      else if (cmd.startswith("REF_LEN:")) {
        cmd.remove(0, String("REF_LEN:").length());

        int firstComma  = cmd.indexOf(',');
        int secondComma = cmd.indexOf(',', firstComma + 1);
        int thirdComma  = cmd.indexOf(',', secondComma + 1);

        dl[0] = cmd.substring(0, firstComma).toFloat() - cableLengths[0];
        dn[0] = length2steps(dl[0]);
        for (uint8_t i = 1; i < 4; ++i) {
          dl[i] = cmd.substring(commas[i - 1] + 1, (i < 3) ? commas[i] : cmd.length()).toFloat() - cableLengths[i];
          dn[i] = length2steps(dl[i]);
          cableLengths[i] = dl[i] + cableLengths[i];
        }
      }
      else {
        Serial.println("ERROR");
        return;
      }
      
      stepParallel(dn);
      Serial.println("OK");
        }
      }
      
  memmove(l_tofs, readTOFs(), sizeof(l_tofs) * sizeof(uint8_t));
  coords_meas = tofs2pcc(l_tofs[0], l_tofs[1], l_tofs[2], l_tofs[3]);
  for (uint8_t i = 0; i < 4; ++i) {
    h[i] = readHelios(i);
  }
  printData();
}

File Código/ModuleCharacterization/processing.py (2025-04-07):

import numpy as np
import pandas as pd
import matplotlib.pyplot as plt

from pathlib import Path
from keras import models as km
from utils import get_data, denormalize, parametric_arc
from helios_kine import iKine, fKine

plt.rcParams['font.family'] = 'Times New Roman'
plt.rcParams['font.size'] = 25

def plot_data(l, h, l_avg, h_avg):
    # Plot the TOF distances
    plt.figure(figsize=(10, 6))
    plt.plot(l[0], label='TOF distance l0')
    plt.plot(l[1], label='TOF distance l1')
    plt.plot(l[2], label='TOF distance l2')
    plt.plot(l[3], label='TOF distance l3')
    
    plt.xlabel('Sample Index')
    plt.ylabel('TOF Distance')
    plt.title('Evolution of TOF Distances')
    plt.legend()
    plt.grid(True)

    # Plot the Helios measurements
    plt.figure(figsize=(10, 6))
    plt.plot(h[0], label='Helios measurement 0')
    plt.plot(h[1], label='Helios measurement 1')
    plt.plot(h[2], label='Helios measurement 2')
    plt.plot(h[3], label='Helios measurement 3')

    plt.xlabel('Sample Index')
    plt.ylabel('Helios Measurement')
    plt.title('Evolution of Helios Measurements')
    plt.legend()
    plt.grid(True)

    # Calculate the differential measurements
    diff_l2_l0 = l[2] - l[0]
    diff_l3_l1 = l[3] - l[1]

    # Plot the differential measurements
    plt.figure(figsize=(10, 6))
    plt.plot(diff_l2_l0, label='Differential l2 - l0')
    plt.plot(diff_l3_l1, label='Differential l3 - l1')

    plt.xlabel('Sample Index')
    plt.ylabel('Differential TOF Distance')
    plt.title('Differential TOF Distances')
    plt.legend()
    plt.grid(True)

    # Calculate the differential measurements for Helios
    diff_h2_h0 = h[2] - h[0]
    diff_h3_h1 = h[3] - h[1]

    # Plot the differential measurements for Helios
    plt.figure(figsize=(10, 6))
    plt.plot(diff_h2_h0, label='Differential h2 - h0')
    plt.plot(diff_h3_h1, label='Differential h3 - h1')
    
    plt.xlabel('Sample Index')
    plt.ylabel('Differential Helios Measurement')
    plt.title('Differential Helios Measurements')
    plt.legend()
    plt.grid(True)

if __name__ == '__main__':
    # File path
    file_path = Path('./dataset/250109/0x4A_250109_train.csv')

    # Plot the data
    h, l, h_avg, l_avg, h0, l0 = get_data(file_path)
    #plot_data(l, h, l_avg, h_avg)

    # Load a model and predict the data
    model = km.load_model('models/nn/nn_0x4A_V.keras')

    # Prepare the test data
    x = np.array(h).T
    y = np.array(l).T

    # Predict the output
    predicted_output = pd.DataFrame(model(x))
    predicted_output = np.array([predicted_output[i].tolist() for i in range(len(predicted_output.columns))])

    # Denormalize the output and the test data
    expected_output = denormalize(l, l0, l_avg)
    predicted_output = denormalize(predicted_output, l0, l_avg)

    '''
    # Plot the predicted output vs the expected output
    plt.figure(figsize=(10, 6))

    # Plot the expected output
    plt.subplot(3, 1, 1)
    plt.plot(expected_output[0], label='Expected TOF distance l0')
    plt.plot(expected_output[1], label='Expected TOF distance l1')
    plt.plot(expected_output[2], label='Expected TOF distance l2')
    plt.plot(expected_output[3], label='Expected TOF distance l3')
    plt.ylim(0, 140)
    plt.xlabel('Sample Index')
    plt.ylabel('TOF Distance')
    plt.title('Expected TOF Distances')
    plt.legend()
    plt.grid(True)

    # Plot the predicted output
    plt.subplot(3, 1, 2)
    plt.plot(predicted_output[0], label='Predicted TOF distance l0')
    plt.plot(predicted_output[1], label='Predicted TOF distance l1')
    plt.plot(predicted_output[2], label='Predicted TOF distance l2')
    plt.plot(predicted_output[3], label='Predicted TOF distance l3')
    plt.ylim(0, 140)
    plt.xlabel('Sample Index')
    plt.ylabel('TOF Distance')
    plt.title('Predicted TOF Distances')
    plt.legend()
    plt.grid(True)

    # Plot the error between the expected and the predicted output
    plt.subplot(3, 1, 3)

    for j in range(len(expected_output)):
        e = [abs(expected_output[j][i] - predicted_output[j][i]) for i in range(len(expected_output[0]))]
        plt.plot(e, label='Error l' + str(j))
    
    plt.ylim(0, 140)
    plt.xlabel('Sample Index')
    plt.ylabel('TOF Distance')
    plt.title('Error')
    plt.legend()
    plt.grid(True)
    '''
    
    e = np.zeros((len(expected_output[0]), 1))
    
    theta_expected, phi_expected, length_expected = fKine(np.transpose(expected_output), 100)
    theta_predicted, phi_predicted, length_predicted = fKine(np.transpose(predicted_output), 100)

    # For plotting the 3D points
    fig = plt.figure()
    ax = fig.add_subplot(111, projection='3d')

    xxe = []
    yye = []
    zze = []

    xxp = []
    yyp = []
    zzp = []

    e = np.zeros((len(expected_output[0]), 1))

    for i in range(len(expected_output[0])):
        xe, ye, ze = parametric_arc(length_expected[i], theta_expected[i], phi_expected[i])
        xp, yp, zp = parametric_arc(length_predicted[i], theta_predicted[i], phi_predicted[i])
        # ax.plot(xp, yp, zp, 'k', alpha=0)

        xxe.append(xe[-1])
        yye.append(ye[-1])
        zze.append(ze[-1])

        xxp.append(xp[-1])
        yyp.append(yp[-1])
        zzp.append(zp[-1])

        e[i] = np.sqrt((xe[-1] - xp[-1])**2 + (ye[-1] - yp[-1])**2 + (ze[-1] - zp[-1])**2)

    # Plot the 3D points
    # Color points based on error magnitude
    for i in range(len(expected_output[0])):
        color = plt.cm.RdYlGn(1 - e[i] / np.max(e))  # Red for max error, green for min error
        ax.scatter(xxp[i], yyp[i], zzp[i], color=color, s=20)

    ax.plot(xxe, yye, zze, 'b', alpha=0.5)

    ax.set_xlabel('x (mm)', labelpad=10)
    ax.set_ylabel('y (mm)', labelpad=10)
    ax.set_zlabel('z (mm)', labelpad=10)
    #ax.set_title('3D Plot of Points with Error Coloring')
    ax.set_zlim(30, 60)
    ax.set_box_aspect([1, 1, 1/4])  # Aspect ratio is 1:1:1 (equal)

    print('Mean Error:', np.mean(e))
    
    plt.figure(figsize=(10, 6))
    plt.plot(e, label='Error')
    plt.plot([np.mean(e)] * len(e), label='Mean Error', linestyle='--', color='red')
    plt.xlabel('Sample Index')
    plt.ylabel('Error')
    plt.title('Tip Error')
    plt.grid(True)
    # Add a color bar to the 3D plot
    mappable = plt.cm.ScalarMappable(cmap=plt.cm.RdYlGn.reversed())
    mappable.set_array([min(e), max(e)])
    cbar = plt.colorbar(mappable, ax=ax, shrink=0.8, aspect=10)
    cbar.set_label('Error (mm)')

    plt.show()

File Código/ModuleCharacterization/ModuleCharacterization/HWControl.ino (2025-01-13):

#include "CNC_Shield_UNO.h"

void setupCNC(){
  pinMode(X_STEP, OUTPUT);
  pinMode(Y_STEP, OUTPUT);
  pinMode(Z_STEP, OUTPUT);
  pinMode(A_STEP, OUTPUT);

  pinMode(X_DIR, OUTPUT);
  pinMode(Y_DIR, OUTPUT);
  pinMode(Z_DIR, OUTPUT);
  pinMode(A_DIR, OUTPUT);

  pinMode(MOT_EN, OUTPUT);

  pinMode(X_STOP, INPUT_PULLUP);
  pinMode(Y_STOP, INPUT_PULLUP);
  pinMode(Z_STOP, INPUT_PULLUP);
  
  //...
}

// MOTION CONTROL
// ___________________________

void step(const uint8_t mot, long n) {
  uint8_t dir = (n<0);
  n = abs(n);
  uint8_t stepPin, dirPin;

  switch(mot){
    case X_MOT:
      stepPin = X_STEP;
      dirPin = X_DIR;
      dir = dir ^ X_REVERSE;
      break;

    case Y_MOT:
      stepPin = Y_STEP;
      dirPin = Y_DIR;
      dir = dir ^ Y_REVERSE;
      break;

    case Z_MOT:
      stepPin = Z_STEP;
      dirPin = Z_DIR;
      dir = dir ^ Z_REVERSE;
      break;

    case A_MOT:
      stepPin = A_STEP;
      dirPin = A_DIR;
      dir = dir ^ A_REVERSE;
      break;

    default:
      return -1;
    }
  digitalWrite(dirPin, dir);

  while(n){
    digitalWrite(stepPin, HIGH);
    delayMicroseconds(STEP_DELAY_HIGH);
    digitalWrite(stepPin, LOW);
    delayMicroseconds(STEP_DELAY_LOW);
    --n;
  }
}

void stepParallel(long dn[4])
{ 
  long aux = max(abs(dn[0]), abs(dn[1]));
  long N = max(abs(dn[2]), abs(dn[3]));
  N = max(N,aux);
  float r[4] = {0, 0, 0, 0};
  int   s[4] = {0, 0, 0, 0};

  for (long i=0; i<N; ++i) {
    for(uint8_t j=0; j<4; ++j) {
      r[j] = r[j] + float(dn[j])/(float)N;
      s[j] = floor(r[j]);
      r[j] = r[j] - float(s[j]);

      step(j, s[j]);
    }
  }
}

// SENSOR CONTROL
// ___________________________

uint32_t readHelios(uint8_t i) {
  helios.setInputMultiplexer(ADS122C04_MUX_AIN0_AVSS + i);
  delay(50);

  float n_samples = 10;
  float n_filter = 4.0;
  uint32_t h = helios.readADC();

  for (uint8_t n = 0; n < n_samples; ++n) {
    h = h * (n_filter-1) / n_filter + helios.readADC() / n_filter;
  }

  return h;
}

void tcaSelect(uint8_t i) {
  if (i > 7) return;
  Wire.beginTransmission(TCA_ADDR);
  Wire.write(1 << i);
  Wire.endTransmission();  
}

uint8_t* readTOFs() {
  float n_samples = 20;
  float n_filter = 5.0;
  static uint8_t l_tofs[4] = {0, 0, 0, 0};

  for (uint8_t i = 0; i < 4; ++i) {
    l_tofs[i] = 0;
  }

  for (uint8_t n = 0; n < n_samples; ++n) {
    for (uint8_t i = 0; i < 4; ++i) {
      tcaSelect(i);
      l_tofs[i] = l_tofs[i] * (n_filter-1) / n_filter + tof.readRange() / n_filter;
    }
  }
  
  return l_tofs;
}

uint32_t* readHelios() {
  static uint32_t h[4] = {0, 0, 0, 0};

  for (uint8_t i = 0; i < 4; ++i) {
    h[i] = readHelios(i);
  }

  return h;
}

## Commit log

2022-05-20 Included Initial Tests' files.
    [Carcasa v1.stl, Polea - soportes.stl, Polea v1.stl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]
2022-05-23 Diseño PCB I_075
    [I-075_board.kicad_pcb, I-075_board.sch]
2022-06-05 Datasheet OPA2380 - Amplificador Operacional de Transimpedancia
2022-07-19 Pruebas WaveGuides
    [Helios_PCB.kicad_pcb, Helios_PCB.sch, Hembra_Molde_DiscoEpoxi.stl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]
2022-07-25 Añadidos planos PCB Helios/ Reorganización carpetas
2022-07-25 Helios PCB - Schematic
    [I-075_board.kicad_pcb, I-075_board.sch]
2022-07-25 Helios -Sch Update
    [Helios_PCB.kicad_pcb, Helios_PCB.sch]
2022-07-25 Helios - Added Connectors
    [Helios_PCB.kicad_pcb, Helios_PCB.sch, SFH_2704_20190402_geometry.STEP]
2022-08-03 Helios: VCC routing
    [Helios_PCB.kicad_pcb, Helios_PCB.sch]
2022-08-03 Helios: Top Layer
    [Helios_PCB.kicad_pcb]
2022-08-05 Helios: Bot Layer Sch. (LEDs)
    [Helios_PCB.kicad_pcb, Helios_PCB.kicad_sch]
2022-08-07 Helios: Bot added resistance
    [Helios_PCB.kicad_pcb, Helios_PCB.kicad_sch]
2022-08-07 Revert "Helios: Bot added resistance"
    This reverts commit fc6911670fedaa5f37ce7a3614e7124a21ec9f54.
    [Helios_PCB.kicad_pcb, Helios_PCB.kicad_sch]
2022-08-07 Revert "Helios: Bot Layer Sch. (LEDs)"
    This reverts commit 9546d183d49721b4727ebea9dfcca252323cf9d1.
    [Helios_PCB.kicad_pcb, Helios_PCB.kicad_sch]
2022-08-07 Revert "Revert "Helios: Bot Layer Sch. (LEDs)""
    This reverts commit 1c39eb4d32ef048d6ab329c7f2d04810a34aa3c7.
    [Helios_PCB.kicad_pcb, Helios_PCB.kicad_sch]
2022-08-07 Revert "Revert "Helios: Bot added resistance""
    This reverts commit c4107a20008b53f7fb3aaff954cae4714a0471ec.
    [Helios_PCB.kicad_pcb, Helios_PCB.kicad_sch]
2022-08-07 Helios: arreglados errores plano de tierra
    [Helios_PCB.kicad_pcb]
2022-08-07 Helios: Rev 1
    [Helios_PCB.kicad_pcb]
2022-08-08 Helios: Second Iteration (half pcb)
    [Helios_PCB.kicad_pcb, Helios_PCB.kicad_sch, Helios_PCB.sch]
2022-08-09 Helios: pcb 3dModel (draft)+Render
    [DraftShape.stl, Helios_PCB.kicad_pcb]
2022-09-16 Helios: Second Iter
    [Disk.cfg, HeliosAsm_1.cfg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]
2022-09-18 Helios: Iteration3
    [Helios_PCB-B_Cu.gbr, Helios_PCB-B_Mask.gbr, Helios_PCB-B_Paste.gbr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]
2022-09-18 Helios: Receiver V1.3
    [Helios_PCB_receiver.kicad_pcb]
2022-09-18 Helios: Emitter V1.3
    [Helios_PCB-B_Cu.gbr, Helios_PCB-B_Mask.gbr, Helios_PCB-B_Paste.gbr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]
2022-09-18 Helios: Updated Silkscreen
    [Helios_PCB_receiver.kicad_pcb]
2022-09-19 Helios: Flex Update
    [HeliosAsm_1.cfg]
2022-09-29 Helios: BOM
    [BOM_Helios.xlsx]
2022-10-08 Last changes V1.3
    [Helios_PCB_emitter.kicad_pcb, Helios_PCB_emitter.kicad_sch, Helios_PCB_receiver.kicad_pcb]
2022-10-08 Updated render
    [Helios_PCB_emitter.kicad_pcb, Helios_PCB_receiver.kicad_pcb]
2022-10-29 Second version of Disk_A
    [Disk.cfg]
2022-11-20 Modelo 3D Banco de Pruebas
2022-11-23 Helios_Section: added SPI Slave example
2023-03-13 SPI comms
2023-04-16 Helios Test Board code update
    [HeliosSection.cfg]
2023-04-16 Actuator class
2023-04-16 Sensor Print method
2023-07-26 SPI version
2023-07-26 I2C STABLE VERSION
2023-08-01 Added init method for ActuatorBench
2023-11-04 Added IMU fucntionality for MPU6050 module
2023-11-06 Added IMU PCB, female connection 3d model, assemblies. Error detected: invert connectors in PCB Male
    [AsmRobot.cfg, AsmSection.cfg, AsmSectionFemale.cfg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]
2023-11-14 Helios Panel
    [AsmRobot.cfg, Helios_PCB_emitter.kicad_pcb, Helios_PCB_emitter.kicad_sch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]
2023-11-14 PCBs ready for manufacturing
    [Helios_PCB_female.kicad_pcb, Helios_PCB_female.kicad_sch, Helios_PCB_panel.kicad_pcb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]
2023-11-20 Minor Changes
    [Helios_PCB_emitter-B_Cu.gbr, Helios_PCB_emitter-B_Mask.gbr, Helios_PCB_emitter-B_Paste.gbr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]
2023-11-20 V2.2 - BNO_055 IMU
    [Helios_PCB_female-B_Cu.gbr, Helios_PCB_female-B_Mask.gbr, Helios_PCB_female-B_Paste.gbr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]
2023-11-22 Minor Updates
    [Helios_PCB_panel.kicad_sch]
2023-11-26 Added alluminium motor plate
    [Asm1.cfg, SoporteMotores.stp]
2023-11-27 Updated Nema Pulley actuator
    [Asm1.cfg]
2023-11-28 Major changes: reverted Object Oriented Programming. Implemented multiple section control. PCB bug detected: GPIO34 & GPIO35.
2024-01-08 Generated STL files for pulley actuator
    [Asm1.cfg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]
2024-01-28 Stable version
    [NemaPulley_PETG_2h17.3mf, NemaPulley_x4_PETG_2h17.3mf]
2024-04-02 Pre MicroROS
    [Asm1.cfg]
2024-04-30 Module CHaracterization
    [0x40_240423_1.csv, 0x40_240423_2.csv, 0x40_240423_3.csv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]
2024-08-02 Added render
    [Helios_rcv_00xx.kicad_pcb]
2024-08-03 Renders update
    [Helios_rcv_00xx.kicad_sch]
2024-08-04 Render explosionado
    [Disk.cfg, DraftShape.stl, HeliosAsm_1.cfg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]
2024-08-14 Helios Claw
2024-08-19 Reorganización Modelos3D
    [Adafruit_BNO055_AP214_pin.cfg, Amass_XT30UPB-F.cfg, Amass_XT30UPB-M.cfg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]
2024-08-20 Instrucciones de Instalación MicroROS
2024-08-21 Actualizadas instrucciones de instalación
2024-08-22 Modo de lectura continuo
2024-08-24 Calibración y mejoras IA
    [0x40_1.xlsx, 0x40_2 - copia.xlsx, 0x40_2.xlsx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]
2024-08-26 IA reentrenada
    [0x40_2 - copia.xlsx, 0x40_240423_1.csv, 0x40_240423_2.csv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]
2024-08-27 Updated sensor reading
2024-08-29 Actualización de los modelos de IA
    [0x40_1.xlsx, 0x40_2.xlsx, 0x40_240823_1.csv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]
2024-08-30 Actualizado script de análisis
2024-09-05 Pruebas de funcionamiento
2024-09-05 Añadidas instrucciones de instalación
2024-12-02 IMU Scan
2024-12-06 Caracterización con TOFs
    [data.csv]
2024-12-06 Update W
    [CE3PRO_worm_gear.3mf]
2024-12-10 Processing and filtering of TOF data
    [0x4A_241207_1.csv, 0x4A_241207_2.csv, 0x4A_241207_3.csv]
2024-12-10 Test data
    [0x4A_241207_4.csv]
2025-01-09 Remove brackets
    [0x4A_250109_445_1.csv]
2025-01-13 Trained model V3
    [0x4A_250109_1.csv, 0x4A_250109_2.csv, 0x4A_250109_3.csv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]
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2025-01-14 MAE for each PCC Parameter
    [abs_error_phi.csv]
2025-04-07 Añadido filtro de media a L
    [0x4A_250109_test_corrected.csv, 0x4A_250109_train_corrected.csv, Helios_Module.cfg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]
2025-04-30 Update proyecto ESP32 to use WiFi
2025-06-03 nodes to plot sensors and calibrate
2025-06-24 added first version of reversed kinematic node and visual
2025-07-07 Inversed kinematic node (in helios_IK_3)
2025-07-21 first version reversed kinematic (to correct)
